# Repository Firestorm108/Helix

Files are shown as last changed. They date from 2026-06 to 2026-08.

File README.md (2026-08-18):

# Helix

An automatic coil winding machine for high voltage transformers, electromagnetics, motors, etc. The combination of the leadscrew controlled spool holder and aligning/tensioning system with the precise TMC2209 controlled stepper spinner ensures even winding across every layer.
The device aims to reduce long hours spent hand winding crappy transformers so that prototyping is quick and efficient. The all-in-one control board has integrated stepper drivers and hooks up to the LCD/rotary encoder based control panel. 
It is easily reprogrammable with USB-C. With a small <75mmx75mm footprint, it fits nicely into the enclosure.

Demo Video: https://youtube.com/shorts/A1r3ZOApkCI?si=vdlbSpJHiryxB_zt

## Main Features 

- Automatic alignment
- Software defined sensing
- High speeds and precision
- Easy reprogrammability + control panel
- Small, portable design
- Custom control board
- Anti-overlap protection

# Pictures


Screenshot 2026-06-07 at 9 40 56 AM
Screenshot 2026-06-07 at 9 41 41 AM

# Helix BOM
*You can find the spreadsheet version here: https://docs.google.com/spreadsheets/d/1YcLF46WpMoUjMdwvhuiZ--BbrOf5m03kofhXg6CQ6rc/edit?usp=sharing

## Electronics

| Item |  Cost |
| --- | ----: |
| JLCPCB + Assembly (2 PCBs) | $80 |
| Pin Headers | $3.00 |
| 2x1 Screw Terminals | $3 |
| DC Barrel Jack | $2 |
| White LCD w/ I2C | $4 |
| Rotary Encoder | $4 |
| 3× TMC2209 Drivers | $9 |
| 2× Stepper Motors | $12 |
| 24V 5A Power Supply | $13 |
| USB-C Power Transfer Board | $2 |
| LM7805 Voltage Regulator | $2 |
| Backup Devboard *(in case of PCB failure)* | $3 |
| Backup 5V Regulator *(in case of PCB failure)* | $3 |
| 330µF 35V Capacitor | $3 |
| Jumpers | $4 |

## Hardware

| Item | Cost |
| --- | ---: |
| M3 Standoffs (10 mm) | $2 |
| M2 Standoffs (6 mm) | $2 |
| 8 mm M3 Screws | $1 |
| 8 mm M2 Screws | $1 |
| TO-220 Heatsink | $2 |
| 300 mm 2020 Aluminum Extrusions |  $14 |
| 150 mm 2020 Aluminum Extrusions |  $19 |
| Corner Brackets |  $20 |
| 5 mm → 8 mm Couplers (2×) | $5 |
| 250 mm 8 mm Rod | $5 |
| 608 Bearings | $7 |
| 250 mm T8 (2 mm Lead) Leadscrew w/ Nut | $9 |
| M5 20 mm Thumbscrew | $3 |
| 1 mm × 8 mm Spring | $4 |

## Cost Summary

| Category | Cost |
| --- | ---: |
| Electronics | $147 |
| Hardware | $94 |
| **Total** | **$241** |

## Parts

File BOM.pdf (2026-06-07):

Item | Price | Link
JLCPCB + Assembly (2 PCBs) | $80 | jlcpcb.com | ELECTRONICS
Pin Headers | $3.00 | https://www.aliexpress.us/item/3256808516771109.html
2x1 Screw Terminals | $3 | https://www.aliexpress.us/item/2255800681269043.html
DC Barrel Jack | $2 | https://www.aliexpress.us/item/2255800284537247.html
White LCD w/ I2C | $4 | https://www.aliexpress.us/item/3256811461891449.html
Rotary Encoder | $4 | https://www.aliexpress.us/item/2251832853007216.html
3 TMC2209s | $9 | https://www.aliexpress.us/item/3256808770530741.html
2 Stepper Motors | $12 | https://www.aliexpress.us/item/3256803688622110.html
24V 5A PSU | $13 | https://www.amazon.com/Power-Supply-LeTaoXing-Adapter-Charger/dp/B08HQR39M4/
Power Transfer USBC | $2 | https://www.aliexpress.us/item/3256805949121880.html
LM7805 Voltage Regulator | $2 | https://www.aliexpress.us/item/3256805383272920.html
Backup Devboard | $3 | https://www.aliexpress.us/item/3256805999451586.html | *In case of PCB failure
Backup 5V Regulator | $3 | https://www.aliexpress.us/item/3256808071645977.html | *In case of PCB failure
Jumpers | $4 | https://www.aliexpress.us/item/2255800397096876.html
M3 Standoffs (10mm) | $2 | https://www.aliexpress.us/item/3256808099562622.html | HARDWARE
M2 Standoffs (6mm) | $2 | https://www.aliexpress.us/item/3256802766024100.html
8mm M3 Screws | $1 | https://www.aliexpress.us/item/3256804345288240.html
8mm M2 Screws | $1 | https://www.aliexpress.us/item/3256804345288240.html
TO220 Heatsink | $2 | https://www.aliexpress.us/item/3256802579959002.html
300m 2020 Extrusions | $14 | https://www.amazon.com/Tsnamay-Aluminum-Extrusion-European-Standard/dp/B0C4311T3P/
150mm 2020 Extrusions | $19 | https://www.amazon.com/SeekLiny-Aluminum-Extrusion-European-Industrial/dp/B0CQSBS2F7/
Corner Brackets | $20 | https://www.amazon.com/Corner-Brackets-Aluminum-Extrusion-Profile/dp/B09YQ1S9NQ/
5mm to 8mm Couplers (2) | $5 | https://www.aliexpress.us/item/3256806935585490.html?
250mm 8mm Rod | $5 | https://www.aliexpress.us/item/3256803408413649.html
608 Bearings | $7 | https://www.aliexpress.us/item/3256806840177845.html
250mm T8 (2mm) Leadscrew w/ Nu | $9 | https://www.aliexpress.us/item/3256805576723890.html
M5 20mm Thumbscrew | $3 | https://www.aliexpress.us/item/3256808128334676.html
1mm / 8mm Spring | $4 | https://www.aliexpress.us/item/3256808666666899.html
Total: | $238

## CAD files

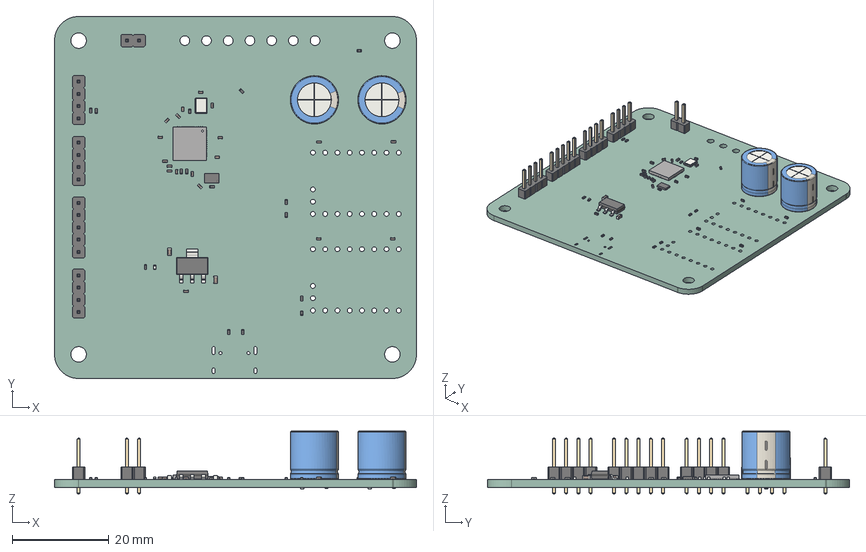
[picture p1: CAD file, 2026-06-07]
PCBs/Helix.step
75.0 x 75.0 x 13.0 mm
C_0402_1005Metric x 19
PinHeader_1x04_P254mm_Vertical x 3
QFN_56_1EP_7x7mm_P04mm_EP32x32mm
CP_Radial_D100mm_P500mm x 2
R_0402_1005Metric x 15
C_0603_1608Metric x 2
Crystal_SMD_3225-4Pin_3.2x2.5mm
LED_0402_1005Metric
SOT_223
PinHeader_1x05_P254mm_Vertical
PinHeader_1x02_P254mm_Vertical
Winbond_USON-8-1EP_3x2mm_P0.5mm_EP0.2x1.6mm
Helix_PCB

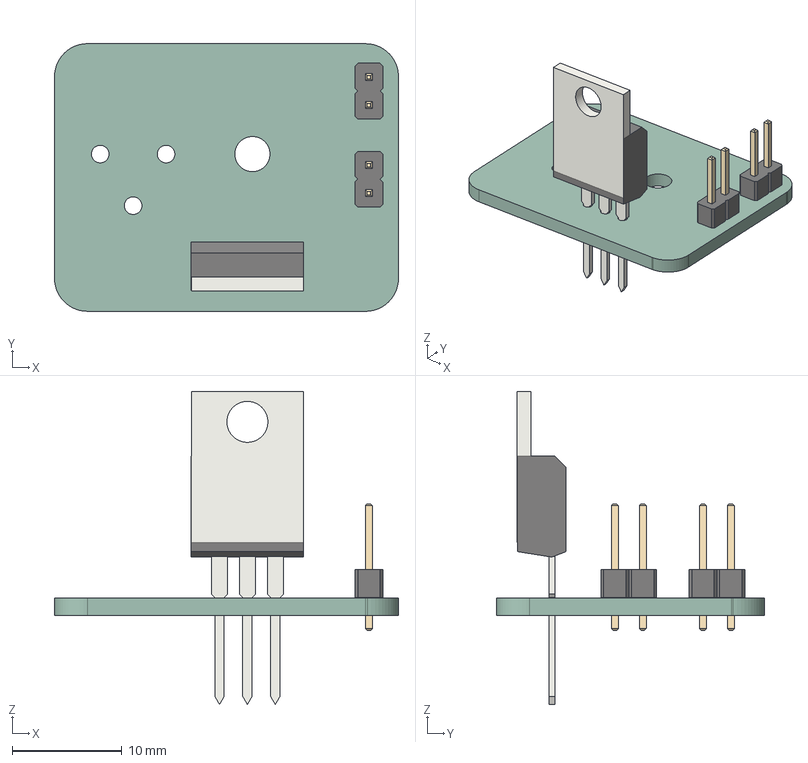
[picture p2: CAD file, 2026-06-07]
PCBs/PowerDelivery/PowerDelivery.step
31.3 x 24.4 x 28.5 mm
PinHeader_1x02_P254mm_Vertical x 2
TO-220-3_Vertical
PowerDelivery_PCB

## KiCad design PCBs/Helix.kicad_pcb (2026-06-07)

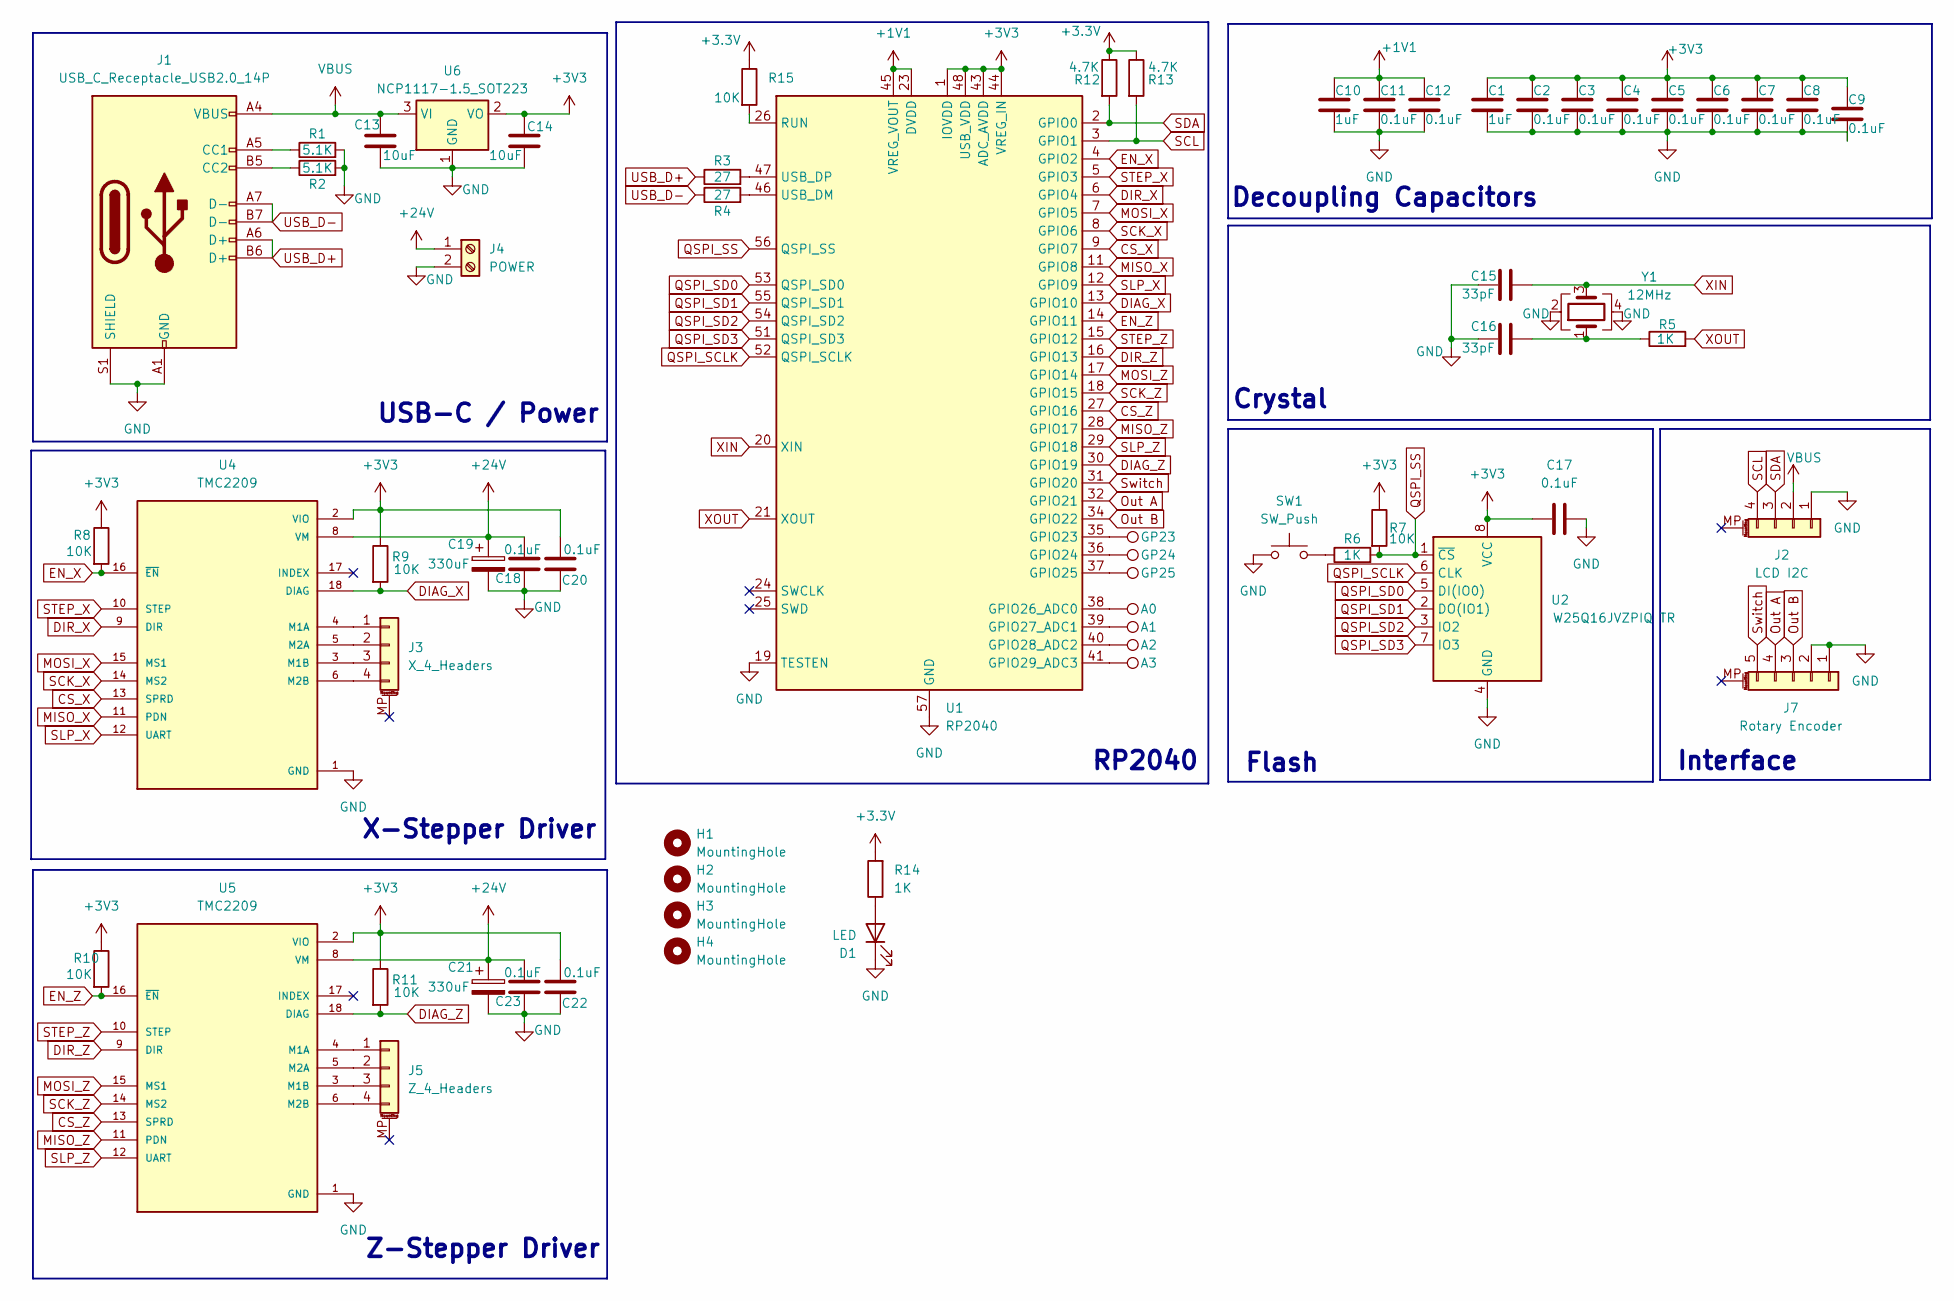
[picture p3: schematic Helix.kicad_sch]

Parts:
A0, A1, A2, A3: TestPoint; TestPoint_Plated_Hole_D2.0mm
C1, C10: 1uF; C_0402_1005Metric
C2, C3, C4, C5, C6, C7, C8, C9, C11, C12, C17, C18, C20, C22, C23: 0.1uF; C_0402_1005Metric
C13, C14: 10uF; C_0603_1608Metric
C15, C16: 33pF; C_0402_1005Metric
C19, C21: 330uF; CP_Radial_D10.0mm_P5.00mm
D1: LED; LED_0402_1005Metric
GP23, GP24, GP25: TestPoint; TestPoint_Plated_Hole_D2.0mm
H1, H2, H3, H4: MountingHole; MountingHole_3.2mm_M3
J1: USB_C_Receptacle_USB2.0_14P; USB_C_Receptacle_HRO_TYPE-C-31-M-12
J2: LCD I2C; PinHeader_1x04_P2.54mm_Vertical
J3: X_4_Headers; PinHeader_1x04_P2.54mm_Vertical
J4: POWER; PinHeader_1x02_P2.54mm_Vertical
J5: Z_4_Headers; PinHeader_1x04_P2.54mm_Vertical
J7: Rotary Encoder; PinHeader_1x05_P2.54mm_Vertical
R1, R2: 5.1K; R_0402_1005Metric
R3, R4: 27; R_0402_1005Metric
R5, R6, R14: 1K; R_0402_1005Metric
R7, R8, R9, R10, R11, R15: 10K; R_0402_1005Metric
R12, R13: 4.7K; R_0402_1005Metric
SW1: SW_Push; SW_Push_SPST_NO_Alps_SKRK
U1: RP2040; QFN-56-1EP_7x7mm_P0.4mm_EP3.2x3.2mm
U2: W25Q16JVZPIQ TR; Winbond_USON-8-1EP_3x2mm_P0.5mm_EP0.2x1.6mm
U4, U5: TMC2209; MODULE_TMC2209_SILENTSTEPSTICK; PARTREV 1.20
U6: NCP1117-1.5_SOT223; SOT-223-3_TabPin2
Y1: 12MHz; Crystal_SMD_3225-4Pin_3.2x2.5mm

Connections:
+1V1: C10.1, C11.1, C12.1, U1.23 (DVDD), U1.45 (VREG_VOUT), U1.50 (DVDD)
+3.3V: R12.1, R13.1, R14.2, R15.1
+3V3: C1.1, C2.1, C3.1, C4.1, C5.1, C6.1, C7.1, C8.1, C9.1, C14.1, C17.1, C18.2, C23.2, R7.1, R8.1, R9.1, R10.1, R11.1, U1.1 (IOVDD), U1.10 (IOVDD), U1.22 (IOVDD), U1.33 (IOVDD), U1.42 (IOVDD), U1.43 (ADC_AVDD), U1.44 (VREG_IN), U1.48 (USB_VDD), U1.49 (IOVDD), U2.8 (VCC), U4.2 (VIO), U5.2 (VIO), U6.2 (VO)
+24V: C19.1, C20.2, C21.1, C22.2, J4.1, U4.8 (VM), U5.8 (VM)
CS_X: U1.9 (GPIO7), U4.13 (SPRD)
CS_Z: U1.27 (GPIO16), U5.13 (SPRD)
DIAG_X: R9.2, U1.13 (GPIO10), U4.18 (DIAG)
DIAG_Z: R11.2, U1.30 (GPIO19), U5.18 (DIAG)
DIR_X: U1.6 (GPIO4), U4.9 (DIR)
DIR_Z: U1.16 (GPIO13), U5.9 (DIR)
EN_X: R8.2, U1.4 (GPIO2), U4.16 (~EN)
EN_Z: R10.2, U1.14 (GPIO11), U5.16 (~EN)
GND: C1.2, C2.2, C3.2, C4.2, C5.2, C6.2, C7.2, C8.2, C9.2, C10.2, C11.2, C12.2, C13.2, C14.2, C15.1, C16.1, C17.2, C18.1, C19.2, C20.1, C21.2, C22.1, C23.1, D1.1 (K), J1.A1 (GND), J1.A12 (GND), J1.B1 (GND), J1.B12 (GND), J1.S1 (SHIELD), J2.1, J4.2, J7.1, J7.2, R1.2, R2.2, SW1.1, U1.19 (TESTEN), U1.57 (GND), U2.4 (GND), U4.1 (GND), U4.7 (GND), U5.1 (GND), U5.7 (GND), U6.1 (GND), Y1.2, Y1.4
MISO_X: U1.11 (GPIO8), U4.11 (PDN)
MISO_Z: U1.28 (GPIO17), U5.11 (PDN)
MOSI_X: U1.7 (GPIO5), U4.15 (MS1)
MOSI_Z: U1.17 (GPIO14), U5.15 (MS1)
unnamed: C16.2, R5.1, Y1.1
unnamed: D1.2 (A), R14.1
unnamed: J1.A5 (CC1), R1.1
unnamed: J1.B5 (CC2), R2.1
unnamed: J3.1, U4.4 (M1A)
unnamed: J3.2, U4.5 (M2A)
unnamed: J3.3, U4.3 (M1B)
unnamed: J3.4, U4.6 (M2B)
unnamed: J5.1, U5.4 (M1A)
unnamed: J5.2, U5.5 (M2A)
unnamed: J5.3, U5.3 (M1B)
unnamed: J5.4, U5.6 (M2B)
unnamed: R6.1, SW1.2
unnamed: GP23.1, U1.35 (GPIO23)
unnamed: GP24.1, U1.36 (GPIO24)
unnamed: GP25.1, U1.37 (GPIO25)
unnamed: A0.1, U1.38 (GPIO26_ADC0)
unnamed: A1.1, U1.39 (GPIO27_ADC1)
unnamed: A2.1, U1.40 (GPIO28_ADC2)
unnamed: A3.1, U1.41 (GPIO29_ADC3)
unnamed: R15.2, U1.26 (RUN)
unnamed: R4.2, U1.46 (USB_DM)
unnamed: R3.2, U1.47 (USB_DP)
Out A: J7.4, U1.32 (GPIO21)
Out B: J7.3, U1.34 (GPIO22)
QSPI_SCLK: U1.52 (QSPI_SCLK), U2.6 (CLK)
QSPI_SD0: U1.53 (QSPI_SD0), U2.5 (DI(IO0))
QSPI_SD1: U1.55 (QSPI_SD1), U2.2 (DO(IO1))
QSPI_SD2: U1.54 (QSPI_SD2), U2.3 (IO2)
QSPI_SD3: U1.51 (QSPI_SD3), U2.7 (IO3)
QSPI_SS: R6.2, R7.2, U1.56 (QSPI_SS), U2.1 (~CS)
SCK_X: U1.8 (GPIO6), U4.14 (MS2)
SCK_Z: U1.18 (GPIO15), U5.14 (MS2)
SCL: J2.4, R13.2, U1.3 (GPIO1)
SDA: J2.3, R12.2, U1.2 (GPIO0)
SLP_X: U1.12 (GPIO9), U4.12 (UART)
SLP_Z: U1.29 (GPIO18), U5.12 (UART)
STEP_X: U1.5 (GPIO3), U4.10 (STEP)
STEP_Z: U1.15 (GPIO12), U5.10 (STEP)
Switch: J7.5, U1.31 (GPIO20)
USB_D+: J1.A6 (D+), J1.B6 (D+), R3.1
USB_D-: J1.A7 (D-), J1.B7 (D-), R4.1
VBUS: C13.1, J1.A4 (VBUS), J1.A9 (VBUS), J1.B4 (VBUS), J1.B9 (VBUS), J2.2, U6.3 (VI)
XIN: C15.2, U1.20 (XIN), Y1.3
XOUT: R5.2, U1.21 (XOUT)

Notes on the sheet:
RP2040
USB-C / Power
Crystal
Interface
Decoupling Capacitors
Flash
Z-Stepper Driver
X-Stepper Driver

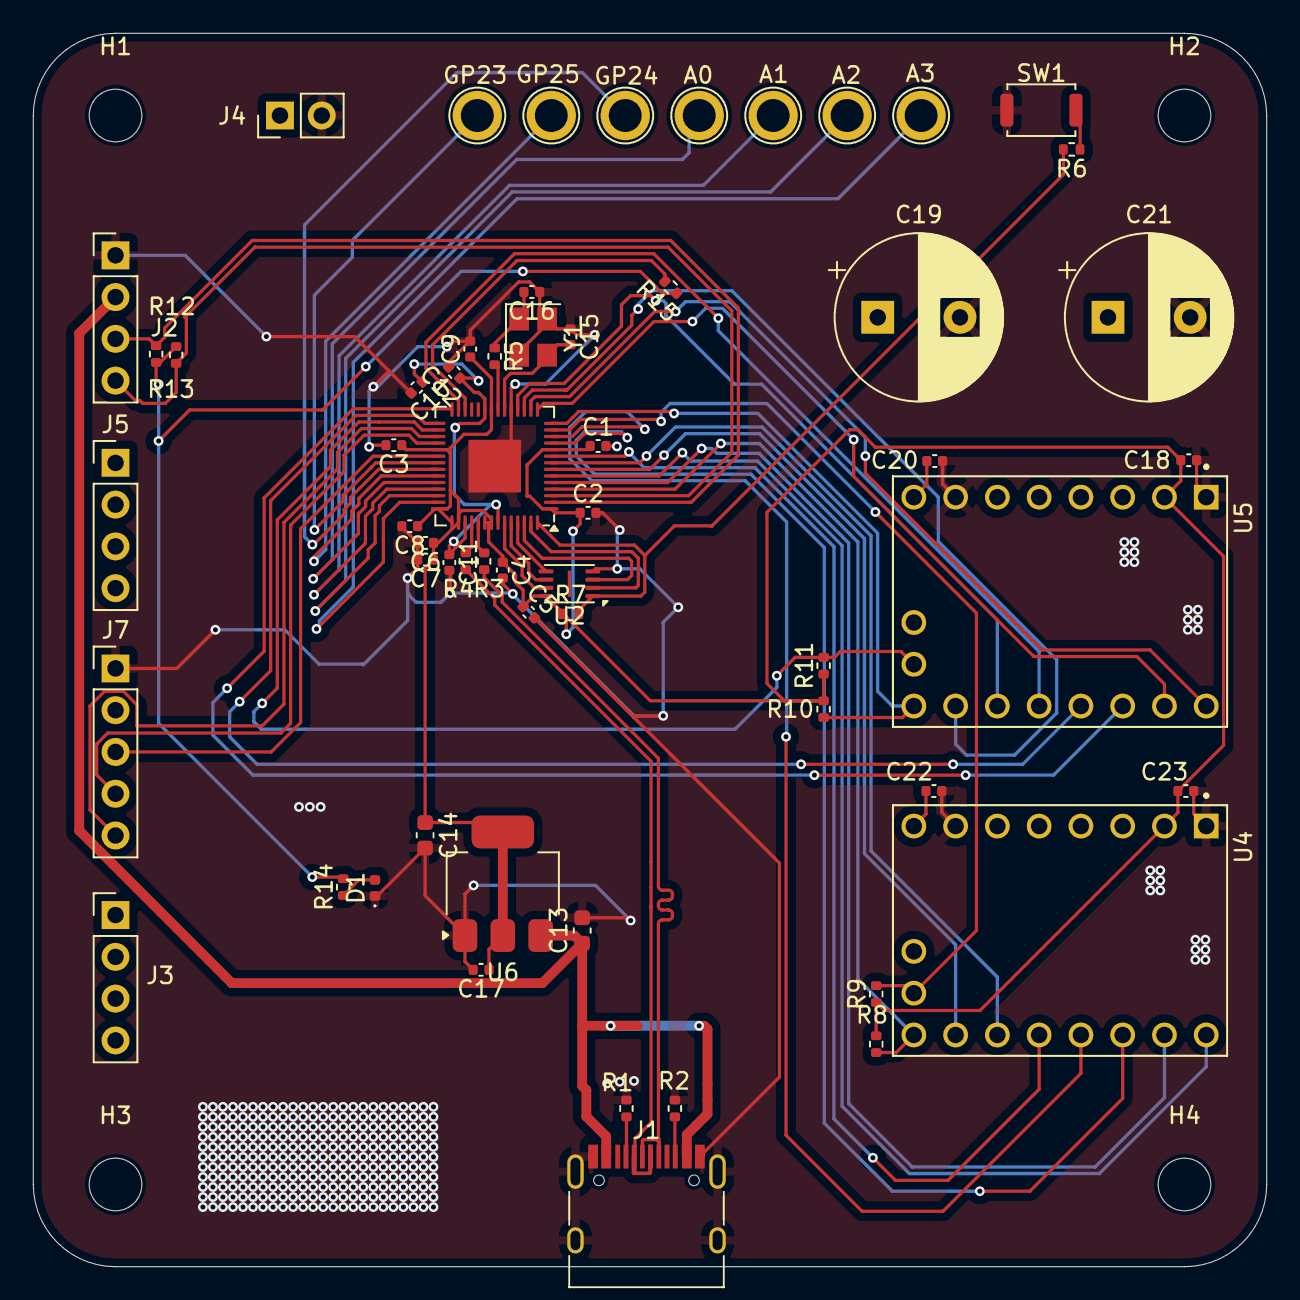
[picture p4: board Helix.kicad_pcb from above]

Board: 4 copper layers, 75.0 x 75.0 mm, 63 parts (0 on the bottom side), 62 nets.

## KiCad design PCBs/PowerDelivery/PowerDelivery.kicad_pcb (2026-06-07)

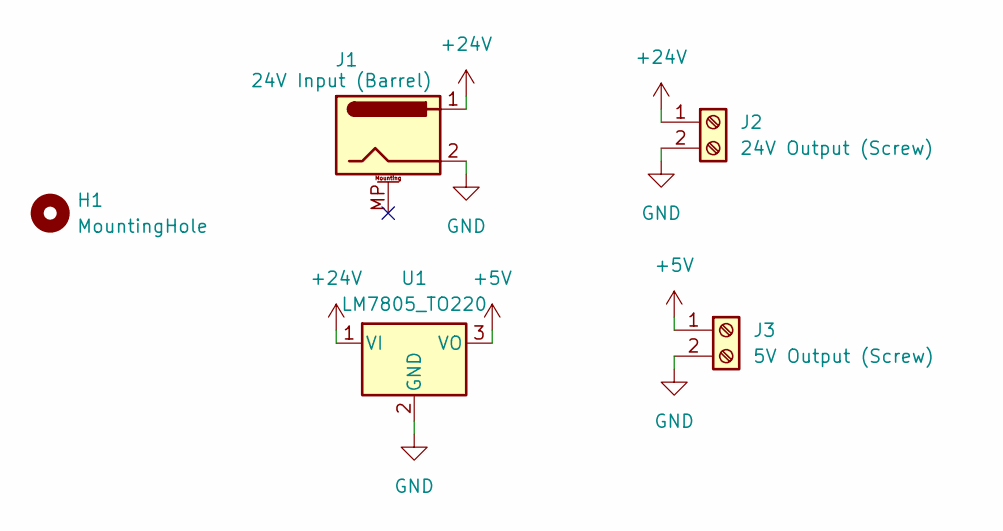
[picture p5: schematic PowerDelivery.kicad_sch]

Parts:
H1: MountingHole; MountingHole_3.2mm_M3
J1: 24V Input (Barrel); BarrelJack_CUI_PJ-102AH_Horizontal
J2: 24V Output (Screw); PinHeader_1x02_P2.54mm_Vertical
J3: 5V Output (Screw); PinHeader_1x02_P2.54mm_Vertical
U1: LM7805_TO220; TO-220-3_Vertical

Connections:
+5V: J3.1, U1.3 (VO)
+24V: J1.1, J2.1, U1.1 (VI)
GND: J1.2, J2.2, J3.2, U1.2 (GND)

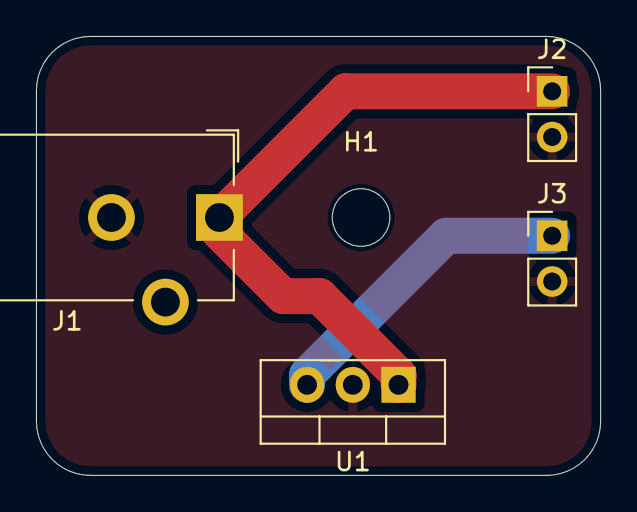
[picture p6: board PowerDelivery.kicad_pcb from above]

Board: 2 copper layers, 31.3 x 24.4 mm, 5 parts (0 on the bottom side), 3 nets.

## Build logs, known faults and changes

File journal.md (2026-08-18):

---
title: "Helix"
author: "Sidd"
description: "Coil Winder"
created_at: "2026-06-07"
total_time: "48 Hours"
---

# May 19th 2026: Initial CAD

I made the y axis and frame of the machine. The steppers, 750mm leadscrews, pillow bearings, and couplers were all placed. As well as the extrusions and corner brackets. This is for adjustment of pipe size and the movement of the coil throughout the length of the coil. However, I am not currently happy with the design and I also think this will be problematic to bring to open sauce. I think that it would be much better to change this to only making stuff like toroids, gate drive transformers, and especially flyback transformers. Winding entire tesla coil secondaries might not be ideal.



Time Spent: 4 Hours

# May 20th 2026: Motherboard Schematic

I decided to base the whole machine off the RP2040 chip, since I don't need any wireless communication and the control should be fairly simple. I started out by making the schematic for the core of the motherboard. So the flash, USB C, MCU, crystal, and caps. Screenshot 2026-05-20 at 4 57 18 PM

After that I added in the two stepper drivers (both TMC2209s) and the interfacing which is just the LCD and the rotary encoder. I'm not sure what else I would need because it seems a lot of the sensing I need can be done in software using the stepper motors. Motorized tensioning could be cool but it is also something I can do without electronics and I don't want to overcomplicate an already tedious task. I'll probably sleep on it and work on this tomorrow, since it's getting late.Screenshot 2026-05-20 at 8 49 31 PM

Time Spent: 5 Hours

# May 22nd 2026: Motherboard Footprints and Layout

First, I assigned footprints to everything based on LCSC. I really hope everything is correct since if even one part fails then the whole board is down. There's not much more to this, it's just a really mundane and repetitive task.
Screenshot 2026-05-22 at 12 57 51 PM

After that I had more fun doing the layout of the board. That took me a while due to the crazy amount of passives, but I think it's a good looking layout and I'm happy with it.
I also routed the differential pairs of the USB-C since I wanted that to the perfect before I started routing anything else.

Screenshot 2026-05-22 at 10 36 47 PM

Time Spent: 4 Hours

# May 24 2026: Finished routing!

I routed all the signal and power traces, following a rather unconventional layer stackup but I'm okay with it. 3 ground layers and one 24V layer, but it is what it is. It was very challenging to route but I'm very happy with the outcome. 
I'm like 90% certain this board is going to work, since I routed it so meticulously. I'm actually super proud since it looks kinda beautiful.

Screenshot 2026-05-25 at 12 05 39 AM

Here's the 3D image:

Screenshot 2026-05-25 at 12 06 59 AM

Time Spent: 8 Hours

# May 25 2026 (Midnight): A problem

So after making the PCB, I realized that the microcontroller has no power source when the machine is powered by the 24V power supply. It is only powered when it is being programmed. The good news is that it only needs to be programmed once, so the USB-C port can be used for powering it after.
However, there is no inbuilt voltage regulator from 24V to 5V, and there is no space to add it in right now. So, my plan is to make a seperate PCB that handles the power.

So 24V flows in via the power supply. This is outputted on the other side into the PCB, however, there is a linear voltage regulator that bumps it down to 5V as well. This 5V goes to a power only USB C receptacle, which can plug into the board.

Here's a rough sketch:

Screenshot 2026-05-25 at 12 58 07 AM

First I made the schematic, nothing too complex.

Screenshot 2026-05-25 at 1 14 48 AM

Then I just made the PCB and did the footprints

Screenshot 2026-05-25 at 1 41 31 AM

I made sure to do all THT since it would be a huge waste of money to get this assembled. It should be like $2 for the PCB and then a couple cents for the components.

# The Morning

I'm glad to finally be getting to the CAD. I firstly desgined the outer frame, inspired from James Albin. 

Screenshot 2026-05-25 at 10 28 40 AM

After thinking for a while and literally just staring at the screen until I came up with something that worked, I rearranged the frame a bit to accomdate better. Then, made the mechanism for spinning the coil that is being wound with a stepper motor. I made an adapter that mimics a flyback core so that the bobbin may spin well. Additionally, the mounts I made for the bearing is cool since I added a little Helix. I kinda focused a lot on covering up unnecessary stuff so that it doesn't look like a prototype.

Screenshot 2026-05-25 at 11 46 03 AM

Time Spent: 5 Hours

# June 5 2026: Finishing up main mechanics

Today I added in the spooling system, which rotates back and forth on a leadscrew. This movement is constrained with a V wheel plate. So the spool rests on top, with hot swappable spool holders. It then goes through a thumbscrew compression based tensioner which feeds into the coil spinner.

Screenshot 2026-06-05 at 8 45 06 PM

Time Spent: 4 Hours

# June 7 2026: Electronics enclosure + finishing!
I made and mounted all the electronics in an emclosure that mounts to the frame. I would say that was the most annoying part because it was mundane and tedious but its okay because it's done now. In the morning I'll work on polishing up the repo and making a bom and stuff but im going to sleep

Screenshot 2026-06-07 at 1 24 24 AM

Time Spent: 2 Hours

# June 25 2026

Today I got the board and soldered it together! It looks super cool ngl. I did some testing and coding and it seems to be working!



Time Spent: 4 Hours

# June 27 2026

I 3D printed some parts and assembled the frame out of extrusions. I unfortunately had to rebuild it since I forgot to put the V-wheel plate on.


Time Spent: 4 Hours

# June 28 2026

I added the steppers, leadscrews, and more printed parts. It's starting to come together and look rlly cool.


Time Spent: 3 Hours

# June 29 2026

I printed and build and coded the electronics box, but had to replace my board with one of my old CNC boards since mine was tweaking out when it controlled the steppers and made everything vibrate like crazy and I wanted it to be reliable for open sauce.


Time Spent: 5 Hours

# June 30 2025

I finished the build! It works and winds coils. I also added a foam based tensioner which wasn't there originally. 



Time Spent: 4 Hours

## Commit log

2026-01-11 Add temporary BOM for tracking items
    [BOM.csv]
2026-01-14 Add coupler to BOM with link
    [BOM.csv]
